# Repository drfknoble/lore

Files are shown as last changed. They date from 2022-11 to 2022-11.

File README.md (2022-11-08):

# Low-Cost, Open-Source Robot for Education (LORE)










## Introduction

Welcome to my repository for my Low-Cost, Open-Source Robot for Education (LORE) project.

<div>
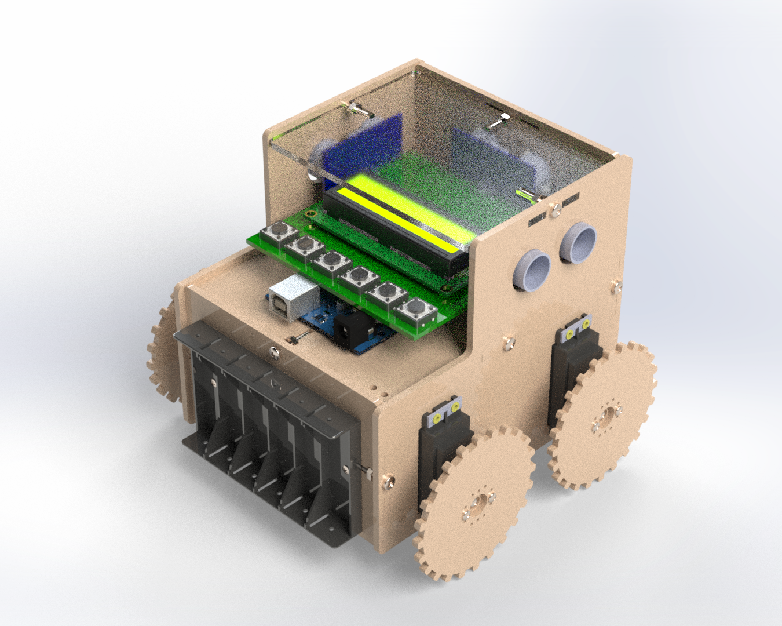
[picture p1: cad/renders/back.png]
    
    
</div>

## Motivation

I started this project because I was approached by the House of Science, a Science, Technology, Engineering, and Mathematics (STEM) organisation in Tauranga, New Zealand, who needed a low-cost, i.e., less than NZD$100.00, platform that could be used to teach robotics.

The problem was: there wasn't anything on the market at met the organisation's needs, so I decided to build one for them.

## Aims

The aims of this project included:
- Developing a low-cost, mobile robot that can be used to teach beginner, intermediate, and advanced students how to program in C++.

## Objectives

The objectives of this project included:
- Creating accessible Computer Aided Design (CAD) files.
- Creating accessible Electronics Design Automation (EDA) files.
- Creating accessible source code and software libraries.
- Creating an easy-to-assemble mobile robot that uses an Arduino microcontroller, servo motors, and ultrasonic sensors.
- Writing clear-to-follow instructions of how to program the mobile robot.

## Repository Structure

The repository is organised as follows:

```console
/lore         
    /cad                          
        /solidworks                    
        /freecad  
        /fabrication
        /renders                     
    /pcb
        /eagle
        /kicad
        /fabrication
    /src
        /beginner
        /intermediate
        /advanced
        /ROBOT
    /doc                      
        /img
        /costing                
        /programming_guide
```

All CAD files can be found in the `/cad` sub-directory. I've included the original SOLIDWORKS files and the open-source equivalents.

All EDA files can be found in the `/pcb` sub-directory. I've included the original Eagle files and the open-source equivalents.

All source code and software libaries are included in the `/src` sub-directory. The `/ROBOT` sub-directory is the Arduino library that is used to program the robot.

Documentation is included in the `/doc` sub-directory.

## Tools Used

I used the following tools in this project:
- SOLIDWORKS and FreeCAD.
- Eagle and KiCAD.
- Microsoft Visual Studio and Arduino Integrated Development IDE (IDE).

Get FreeCAD here: https://www.freecadweb.org/.  
Get KiCAD here: https://www.kicad.org/.  
Get Arduino IDE here: https://www.arduino.cc/en/software.  
Get Visual Studio here: https://visualstudio.microsoft.com/.  

Alternatively, you can use Microsoft Visual Studio Code as the IDE.

Get Code here: https://code.visualstudio.com/.

## Credit

Dr Frazer K. Noble  
http://drfknoble.com

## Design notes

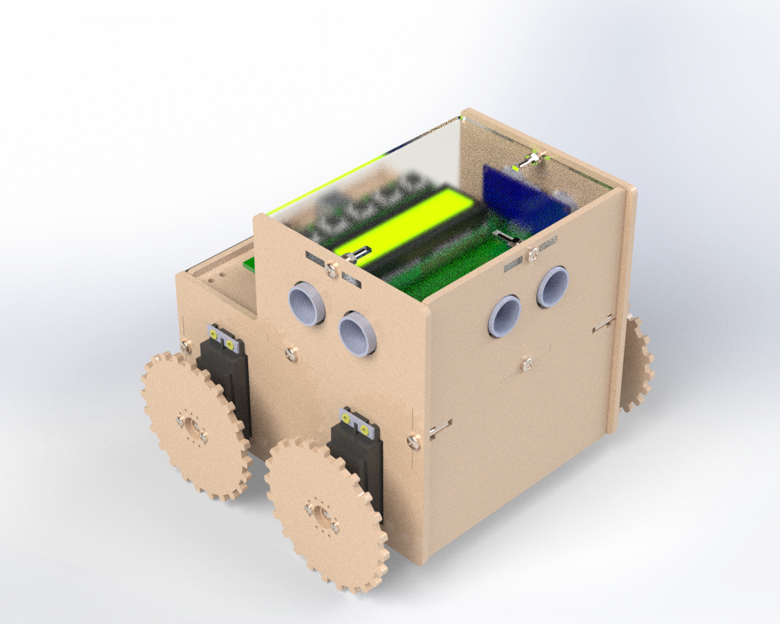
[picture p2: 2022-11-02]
cad/renders/front.png

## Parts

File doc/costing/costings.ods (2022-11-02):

Low-cost Open-source Robotics Education (LORE) kit
Item | Supplier | Number | Unit Cost (NZD) | Total Cost (NZD)
Moxie Mox-M38-360 Motors | Low Price RC | 96 | $5.00 | $480.00
MDF per robot kit | Mitre 10 Mega | 2 | $20.00 | $40.00
LCD 16x02 | Ebay | 30 | $3.00 | $90.00
Arduino Uno Rev. 3 | Ebay | 30 | $12.00 | $360.00
Ultrasonic Sensors | Ebay | 9 | $17.00 | $153.00
Tactile Switch | Ebay | 5 | $4.00 | $20.00
Header Pins | Ebay | 6 | $2.00 | $12.00
DC-DC LM2596 Converter | Ebay | 30 | $2.00 | $60.00
Battery Case | Ebay | 30 | $3.00 | $90.00
PCB | Seed Studio | 1 | $100.00 | $100.00
M3 * 15 Nuts and Bolts | EDL/Mitre 10 Mega | 8 | $5.00 | $40.00
Tools | Mitre 10 Mega | 4 | $10.00 | $40.00
Batteries | The Warehouse | 1 | $40.00 | $40.00
 |  |  | Material Cost: | $1,525.00
Beginner Kits |  | 16 | $35.00 | $560.00 | Cost: | $98.54 | RRP: | $150.00
Intermediate Kits |  | 8 | $20.00 | $160.00 |  | $83.54 |  | $125.00
Advanced Kits |  | 0 | $5.00 | $0.00 |  | $68.54 |  | $100.00
 | Total Kits: | 24 | Time Cost: | $720.00 |  |  | Total Sales: | $3,400.00
 |  |  | Total Cost: | $2,245.00 |  |  | Total Profit: | $1,155.00
Moxie M38-360 Analog Plastic Standard 360° Servo For FPV [MOX-M38-360] - $4.08USD$3.40USD Low Price RC Limited
http://www.lowpricerc.com/product_info.php/moxie-m38-360-analog-plastic-standard-360%C3%82%C2%B0-servo-for-fpv-p-745
Arduino Uno R3 Official Board Rev 3 Sense and Control LEDs Robots Electronics | eBay
http://www.ebay.com/itm/Arduino-Uno-R3-Official-Board-Rev-3-Sense-and-Control-LEDs-Robots-Electronics-/360580350466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
New DC DC LM2596 Step Down Adjustable Power Supply Module Converter DC 1 3V 35V | eBay
http://www.ebay.com/itm/New-DC-DC-LM2596-Step-Down-Adjustable-Power-Supply-Module-Converter-DC-1-3V-35V-/380755874794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
50x Tact Tactile Push Button Switch Momentary DIP Through Hole 4pin 12x12x4 3mm | eBay
http://www.ebay.com/itm/50x-Tact-Tactile-Push-Button-Switch-Momentary-DIP-Through-Hole-4pin-12x12x4-3mm-/281245791277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
10 x Ultrasonic Module HC SR04 Distance Measuring Transducer Sensor for Arduino | eBay
http://www.ebay.com/itm/10-x-Ultrasonic-Module-HC-SR04-Distance-Measuring-Transducer-Sensor-for-Arduino-/130705106799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
10pcs 40pin 2 54mm Single Row Straight Male Pin Header Strip PBC Ardunio | eBay
http://www.ebay.com/itm/10PCS-40Pin-2-54mm-Single-Row-Straight-Male-Pin-Header-Strip-PBC-Ardunio-/180974247480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
AA Battery Case 6XAA 6 AA 9V Battery Holder Battery Box with Wire Plug 5 5 2 1mm | eBay
http://www.ebay.com/itm/AA-Battery-Case-6XAA-6-AA-9V-Battery-Holder-Battery-Box-With-Wire-Plug-5-5-2-1mm-/231103696144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
1602 16x2 HD44780 Character LCD Display Module LCM Blue Blacklight New 2014 | eBay
http://www.ebay.com/itm/1602-16x2-HD44780-Character-LCD-Display-Module-LCM-blue-blacklight-New-2014-/181295337227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
AA Battery Case 6XAA 6 AA 9V Battery Holder Battery Box with Wire Plug 5 5 2 1mm | eBay
http://www.ebay.com/itm/AA-Battery-Case-6XAA-6-AA-9V-Battery-Holder-Battery-Box-With-Wire-Plug-5-5-2-1mm-/231103696144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

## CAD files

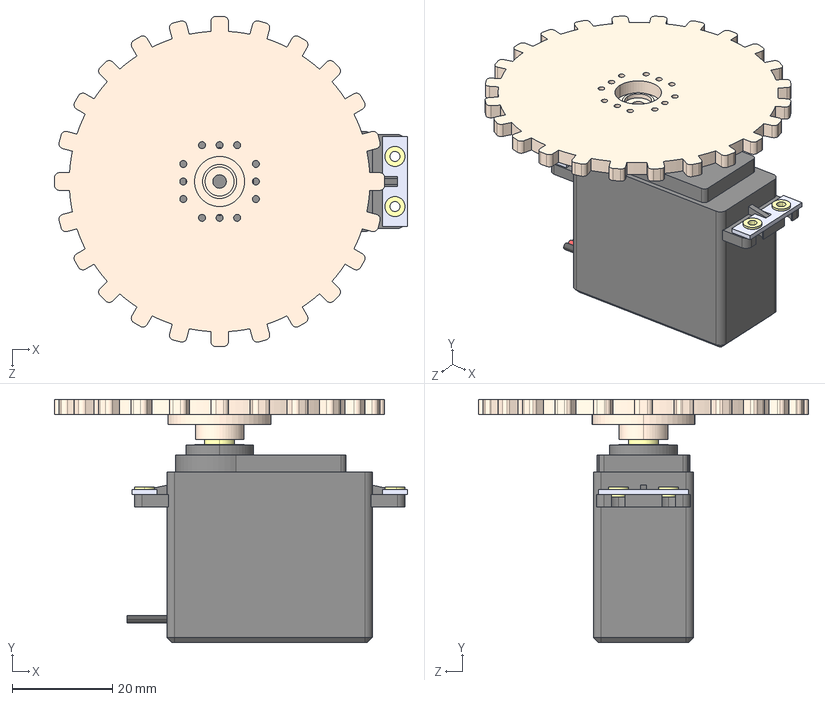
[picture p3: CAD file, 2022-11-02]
cad/freecad/sub_assemblies/motor_assembly.STEP
70.4 x 48.5 x 65.9 mm
servo_motor
servo_eyelet x 4
servo_horn
servo_mounting_rubber x 2
wheel

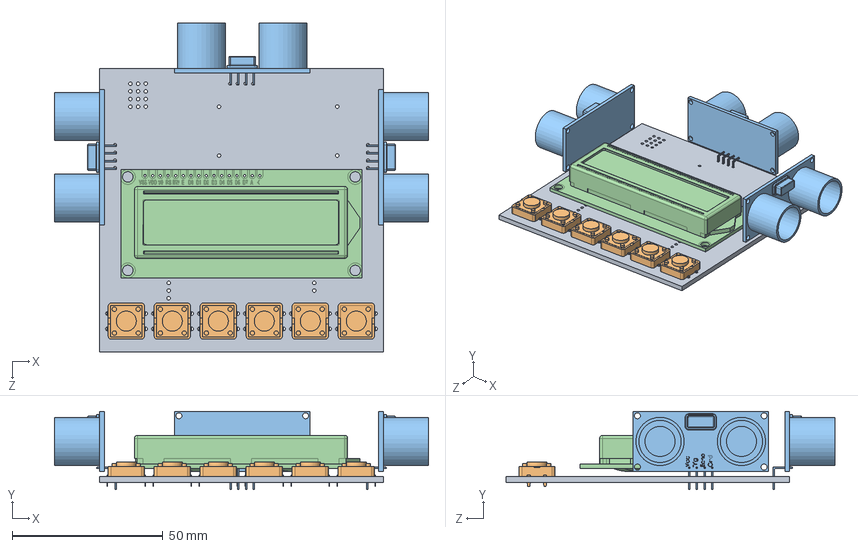
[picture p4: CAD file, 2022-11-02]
cad/solidworks/sub_assemblies/shield_assembly.SLDASM
124.0 x 26.0 x 109.0 mm
pcb
momentary_switch x 6
ultrasonic_sensor x 3
lcd1602

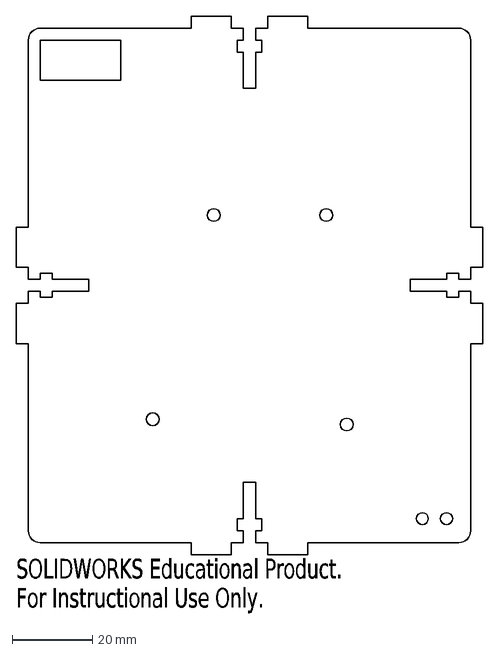
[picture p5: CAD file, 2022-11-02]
cad/fabrication/middle.DXF
SOLIDWORKS Educational Product.
For Instructional Use Only.

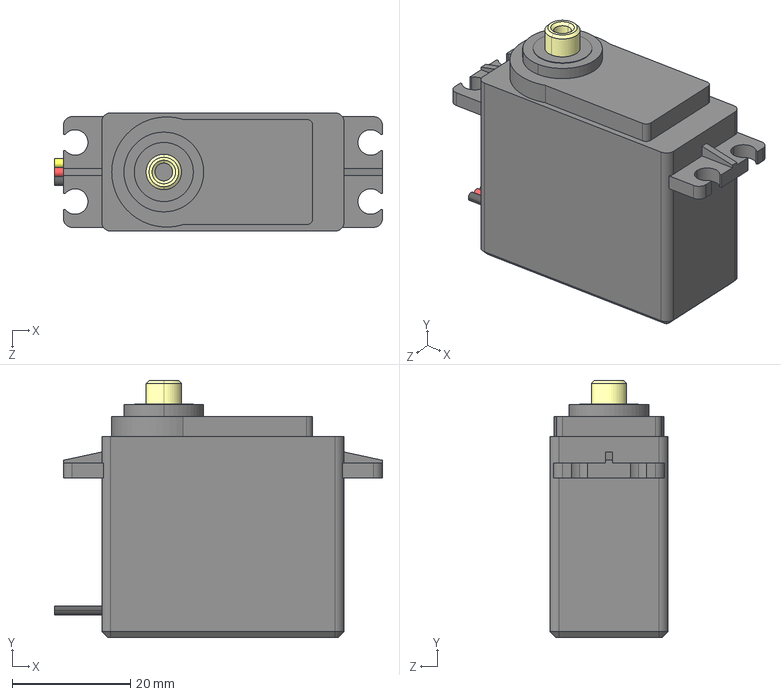
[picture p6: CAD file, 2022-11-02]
cad/freecad/parts/servo_motor.STEP
55.5 x 43.5 x 20.0 mm

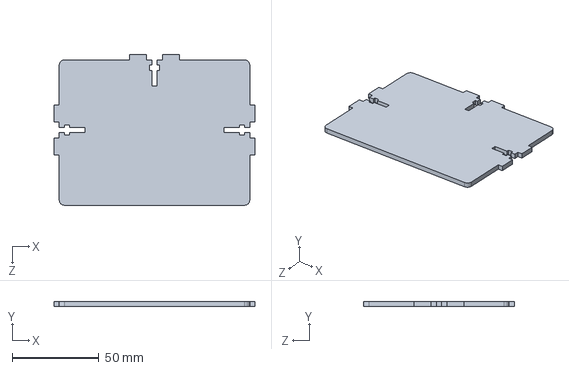
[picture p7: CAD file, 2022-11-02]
cad/solidworks/parts/top.SLDPRT
116.0 x 3.00 x 86.9 mm

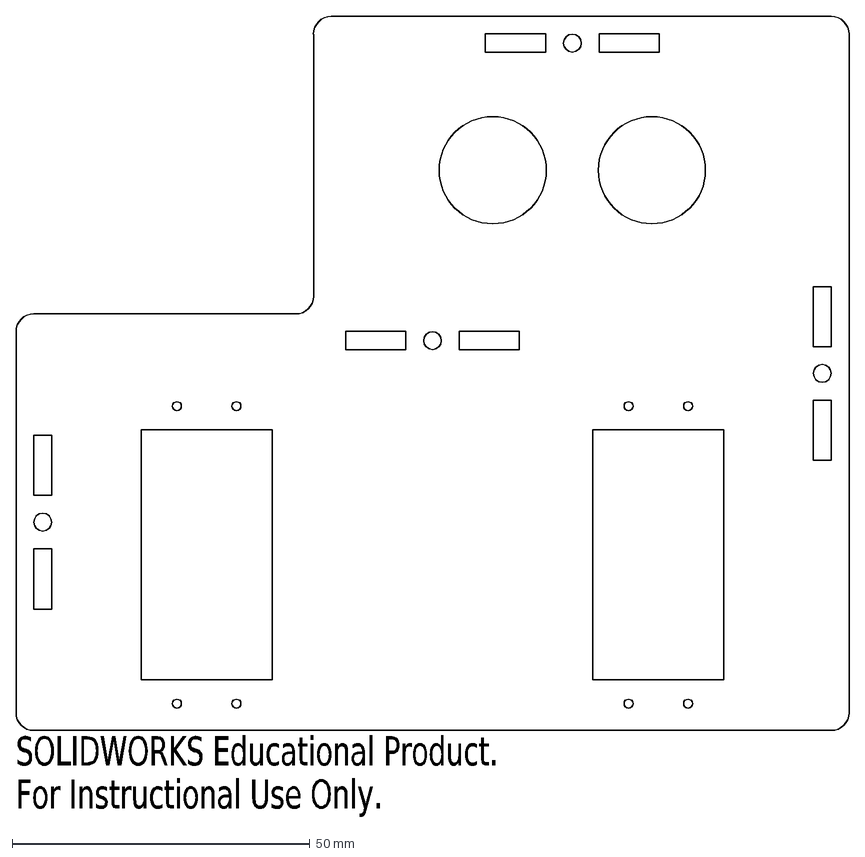
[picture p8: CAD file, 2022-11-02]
cad/fabrication/side.DXF
SOLIDWORKS Educational Product.
For Instructional Use Only.

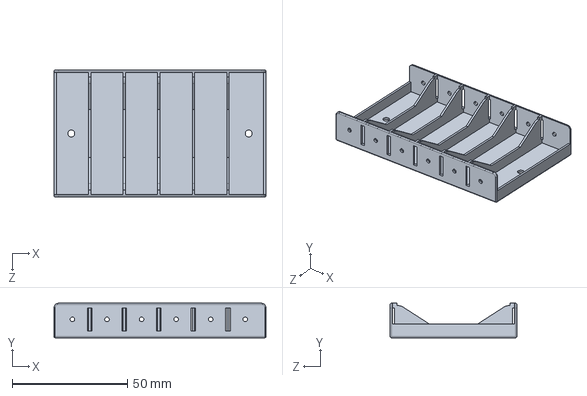
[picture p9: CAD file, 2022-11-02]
cad/freecad/parts/battery_clip.STEP
92.0 x 15.0 x 55.0 mm

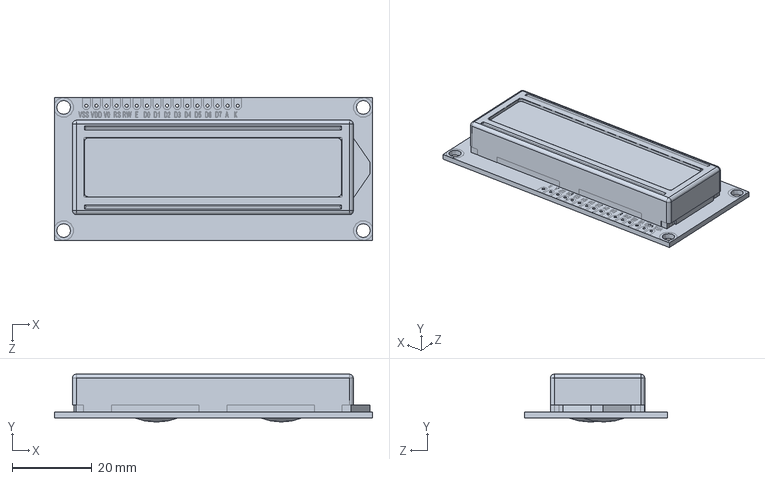
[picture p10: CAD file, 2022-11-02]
cad/solidworks/parts/lcd1602.SLDPRT
80.0 x 12.1 x 36.0 mm

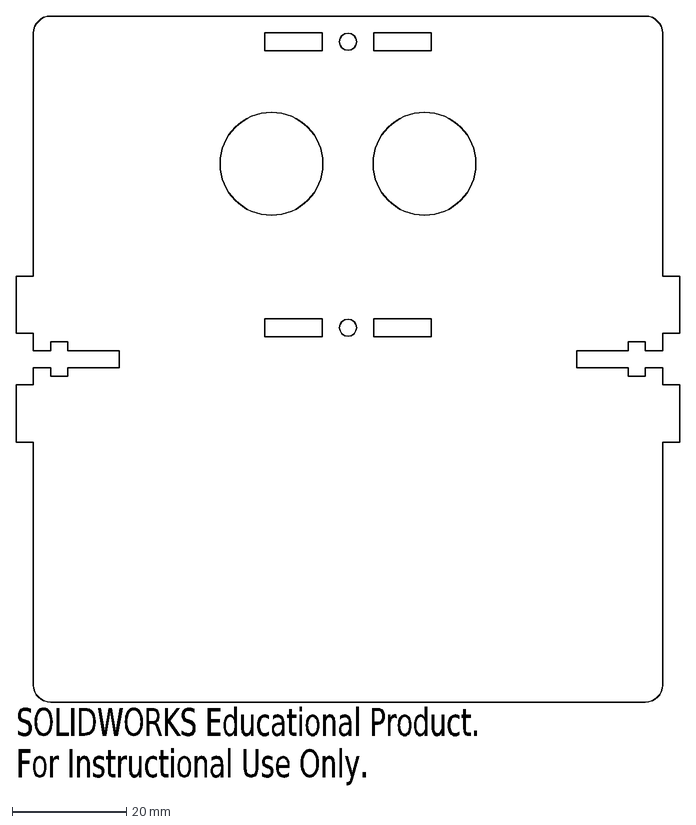
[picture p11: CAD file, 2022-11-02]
cad/fabrication/front.DXF
SOLIDWORKS Educational Product.
For Instructional Use Only.

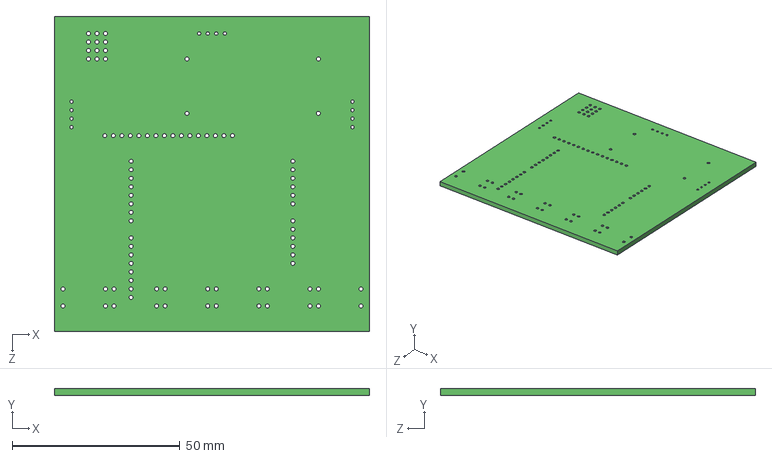
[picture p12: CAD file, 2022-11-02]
cad/freecad/parts/pcb.STEP
94.0 x 2.00 x 94.0 mm

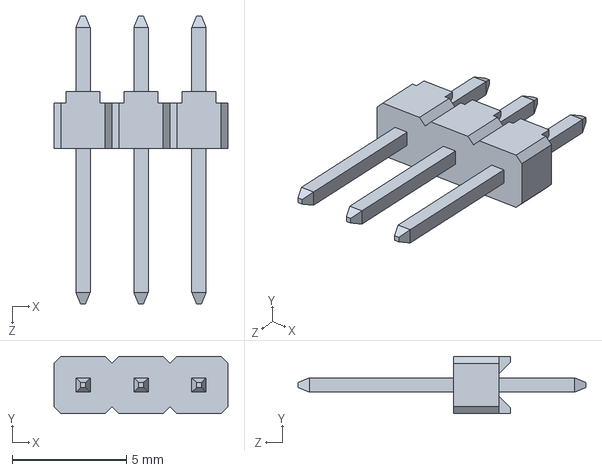
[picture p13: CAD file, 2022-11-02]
cad/solidworks/parts/3_pin_header.SLDPRT
7.62 x 2.50 x 12.6 mm

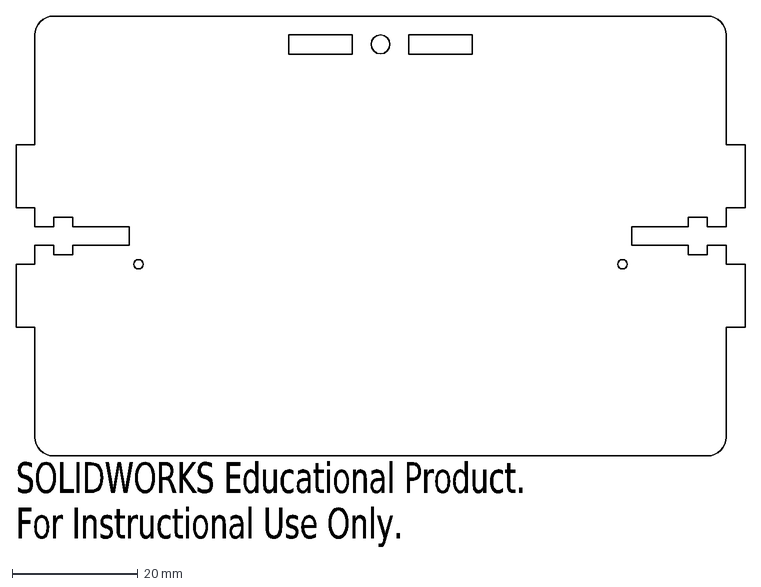
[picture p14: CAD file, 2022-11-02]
cad/fabrication/back.DXF
SOLIDWORKS Educational Product.
For Instructional Use Only.

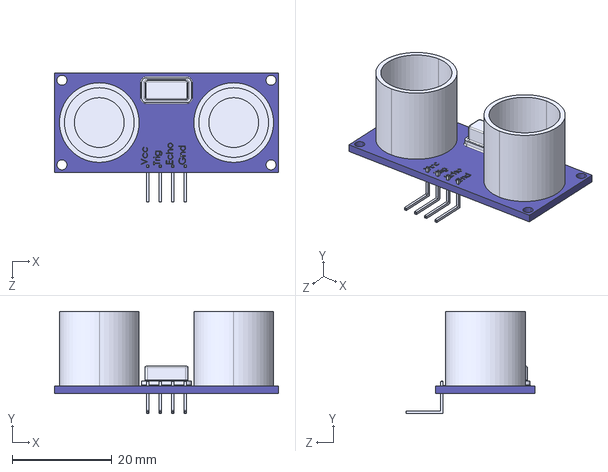
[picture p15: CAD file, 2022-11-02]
cad/freecad/parts/ultrasonic_sensor.STEP
45.0 x 20.5 x 26.0 mm

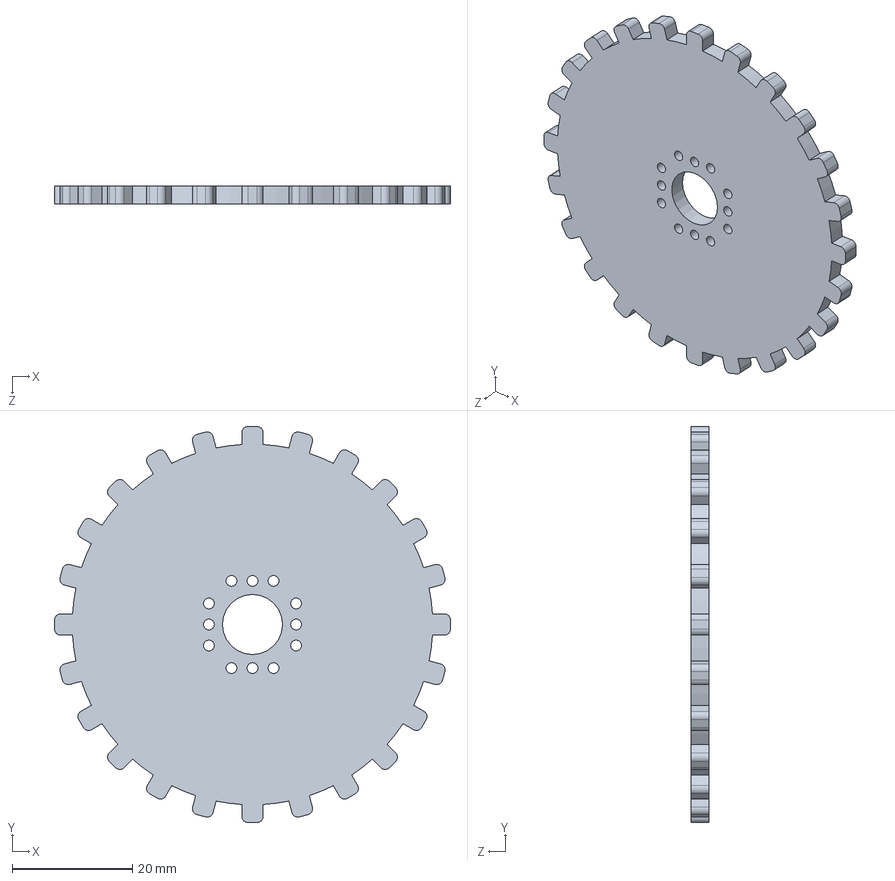
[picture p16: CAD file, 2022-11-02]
cad/solidworks/parts/wheel_alt.sldprt
65.9 x 65.9 x 3.00 mm

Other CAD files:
cad/freecad/parts/servo_eyelet.STEP
cad/freecad/parts/momentary_switch.STEP
cad/freecad/parts/back.STEP
cad/freecad/parts/front.STEP
cad/freecad/parts/middle.STEP
cad/freecad/parts/servo_horn.STEP
cad/freecad/parts/servo_mounting_rubber.STEP
cad/freecad/parts/side.STEP
cad/freecad/parts/wheel.STEP
cad/solidworks/parts/back.SLDPRT
cad/solidworks/parts/battery_clip.SLDPRT
cad/solidworks/parts/front.SLDPRT
cad/solidworks/parts/middle.SLDPRT
cad/solidworks/parts/momentary_switch.SLDPRT
cad/solidworks/parts/pcb.SLDPRT
cad/solidworks/parts/servo_eyelet.SLDPRT
cad/solidworks/parts/servo_horn.SLDPRT
cad/solidworks/parts/servo_motor.SLDPRT
cad/solidworks/parts/servo_mounting_rubber.SLDPRT
cad/solidworks/parts/side.SLDPRT
cad/solidworks/parts/ultrasonic_sensor.SLDPRT
cad/solidworks/parts/wheel.sldprt
cad/solidworks/sub_assemblies/motor_assembly.SLDASM

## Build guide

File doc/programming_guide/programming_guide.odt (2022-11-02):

Disclaimer: Low-cost Open-source Robotics Educational (LORE) kits are provided "as is" with no warranties whatsoever, including any warranty of merchantability, non - infringement, fitness for any particular purpose, or any warranty otherwise arising out of any proposal, specification or sample. LORE kits (and manufacturers and distributors) disclaim all liability, including liability for infringement of any proprietary rights, relating to use of information in any documents and files and software and no license, express or implied, by LORE kits or otherwise, to any intellectual property rights is granted herein. LORE kits (and manufacturers and distributors) assumes no responsibility or liability for any errors or inaccuracies that may appear in any documentation or files or any software that may be provided. The information in any documents or files is furnished for informational use only, is subject to change without notice, and should not be construed as a commitment by LORE kits (and manufacturers and distributors).

# Table of Figures

Figure 1: Beginning Programming Level procedure. 2

Figure 2: Arduino Uno R3 Board 3

Figure 3: Intermediate Programming Level procedure. 6

Figure 4: Advanced Programming Level procedure. 9

# Editions

Edition 1.

Edition 1.01. Added introductory programming examples, i.e. Getting Started. Added additional information regarding new functions, e.g. turn() and setTurnTime().

# Low-Cost Open-Source Robotics Education (LORE) kit Programming Guide:

Programming the LORE robot can be broken into three levels of difficulty:

- Beginner Programming Level. Suitable for students with no programming experience. No computer experience required.
- Intermediate Programming Level. Suitable for students with some programming knowledge. Students should be familiar with computers and how to use an Internet browser, keyboard and mouse.
- Advanced Programming Level. Suitable for students with programming experience in C/C++. Students should be computer literate and familiar with Windows 7/8.

To familiarise students with programming, the following section provides a primer on programming.

# Programming Primer:

There are a number of excellent resources for learning to program, e.g. LearnCpp.com. Here, we provide a very basic, and limited, introduction to some key concepts: variables and functions, which are used in the Intermediate and Advanced Programming Levels.

For a complete introduction to variables and functions, see the tutorials available from LearnCpp:

http://www.learncpp.com.

Variables:

“A variable in C/C++ is a name for a piece of memory that can be used to store information” (C++, 2014). A variable can be thought of as a box, where information can be put.

Here’s an example of declaring an integer variable:

int x = 0;

The variable’s name is x and is set to zero. Keyword int sets the variable type to integer. The equal sign is used to specify what integer x is equal to. The number zero sets x’s value.

For a complete list of variable types, see the following link:

http://en.wikipedia.org/wiki/C_data_types

Functions:

“A function is a sequence of statements designed to do a particular job” (C++, 2014). In C/C++, every program requires a main() function; however, for Arduino boards, there must be a setup() function and a loop() function.

Here’s an example of declaring a function:

void print(char* string) {

Serial.print(string);

}

The function’s name is print. Function print() takes a single parameter: string, which is an array of characters. Function print() calls the print() member function, or method, of an instance of a Serial Port class, Serial. Function print() does not return any value; however, functions can return any standard data type.

# Beginner Programming Level Guide:

The Beginner Programming Level is suitable for students that have no prior knowledge of programming. Programming the LORE robot is done by pressing the PROGRAM button followed by pressing a series of LEFT, RIGHT, FRONT, and BACKWARD directional buttons. Once a program is finished, pressing the SELECT button saves the program. Each time the directional buttons are pressed, the LCD panel will display the button pressed. By default the maximum program size is 50 steps; however, this can be changed. When the program is full, the LCD will display “PROGRAM FULL”. Pressing the SELECT button a second time executes the program. The program will run through each pre-programmed step until it is finished. By default, each step will execute for one second (FORWARD and BACKWARD movements) or 90 ° (LEFT or RIGHT turns). Pressing the SELECT button will re-run the program. Pressing the PROGRAM button again will re-enter programming mode. When re-entering programming mode, the previous program is overwritten.

The following figure (Figure 1) outlines the Beginner Programming Level structure:

Press the PROGRAM button.

Press the PROGRAM button to enter programming mode.

↓

Enter the PROGRAM.

Press the LEFT, RIGHT, FORWARD, or BACKWARD buttons.

Repeat this step till desired movements are loaded.

↓

Press the SELECT button.

Press the SELECT button to save the program.

↓

Press the SELECT button.

Press the SELECT button to run the program.

↓

Wait for program to run.

Figure 1: Beginning Programming Level procedure.

## Beginner Programming Level Example 1:

Consider a student, Marty, who wants to make the LORE robot move forward for 10 seconds, turn left, move forward for two seconds, and then stop.

To program the LORE robot to do this, the student should do the following:

1. Press the PROGRAM button. This will enter programming mode.
2. Press the FORWARD button. This will make the LORE robot move forward for one second.
3. Repeat Step 2 9 more times. Pressing the FORWARD button an additional nine more times will program the robot to move forward for an additional nine seconds.
4. Press the LEFT button. This will make the robot turn 90 ° to the left.
5. Press the FORWARD button. This will make the LORE robot move forward for one second.
6. Repeat Step 5 one more time. Pressing the FORWARD button one more time will program the robot to move forward for an additional one second.
7. Press the SELECT Button.

To run the program, the student should press the SELECT button again.

# Intermediate Programming Level Guide:

The Intermediate Programming Level is suitable for students who have some prior knowledge of programming and are familiar with computers, i.e. able to use a mouse and keyboard for typing and data entry in a Windows 7/8 environment, as well as, browsing the Internet using an Internet browser. Students are provided with a simple set of functions, which they can call to program the robot to move (FORWARD and BACKWARD) and turn 90 ° (LEFT and RIGHT). Students can also access the LORE robot’s FRONT SENSOR, LEFT SENSOR, and RIGHT SENSOR ultrasonic sensors to measure distances from the robot.

## Getting Started:

Before being able to program the robot, students will need to download the Arduino integrated development environment (IDE) and the ROBOT library file. The IDE can be downloaded for free from the following site:

http://arduino.cc/

Browse to the Download section and download the latest, stable version: as of May, 2014 it is version 1.0.5. The Windows Installer will automatically install all the software and drivers necessary to program the LORE robot’s microcontroller: the Arduino Uno. By default the IDE will install to C:\Progam Files\Arduino; however, you may install this to any directory. When installing the Arduino IDE you will need administrator rights to install software and driver. For supplementary instructions on installing the Arduino IDE, refer to the Arduino website.

Once the Arduino IDE is installed, you can make use of a library created for the LORE robot and the Arduino board. Download ROBOT.zip from the following link:

https://sourceforge.net/projects/lorerobotics/files/.

Extract ROBOT.zip to the Arduino user library folder. To extract the file, right click the file and left click Extract All…. By default the Arduino user library folder will be in the default Arduino workspace within the documents directory, e.g. C:\Users\...\Documents\Arduino\libraries (NB. “…” corresponds to the current user name; this will differ from machine to machine).

To use the library, open the Arduino IDE and left click Select>Add Library…>ROBOT. If ROBOT.zip has been extracted to the correct file, the library ROBOT will be listed under the Contributed libraries.

## Programming the Arduino Board:

The Arduino board is a simple-to-use and easy-to-program development board. The LORE robot uses the Uno model (see Figure 2).

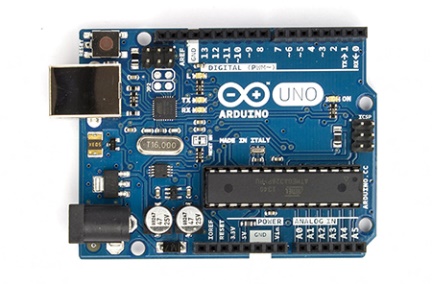
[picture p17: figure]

Figure 2: Arduino Uno R3 Board

For tutorials on programming Arduinos, have a look at the following link:

http://arduino.cc/en/Tutorial/HomePage

At the least, the following code is necessary for programming the Arduino board:

void setup()

{

// put your setup code here, to run once:

}

void loop()

{

// put your main code here, to run repeatedly:

}

The setup() function is called when a sketch starts. Use it to initialize variables, pin modes, start using libraries, etc. The setup function will only run once, after each power up or reset of the Arduino board. After creating a setup() function, which initializes and sets the initial values, the loop() function does precisely what its name suggests, and loops consecutively, allowing your program to change and respond. Use it to actively control the Arduino board. Program logic should be placed in loop(), which will continuously execute the program.

Intermediate Programming Level Tip 1:

When uploading the programme to the LORE robot’s Arduino, you’ll need to identify which COM port to use. Typically COM 1/2 refers to the hardware serial ports on older machines, so you’ll find the Arduino’s COM port will be COM 3 or higher. You can be sure which COM port it is by using Window’s Device Manager. This can be found by pressing the Windows Start key and typing “Device Manager”, then selecting Device Manager under the found items. Browsing to the Ports (COM & LPT) menu and expanding it, you can see what the Arduino’s COM port is.

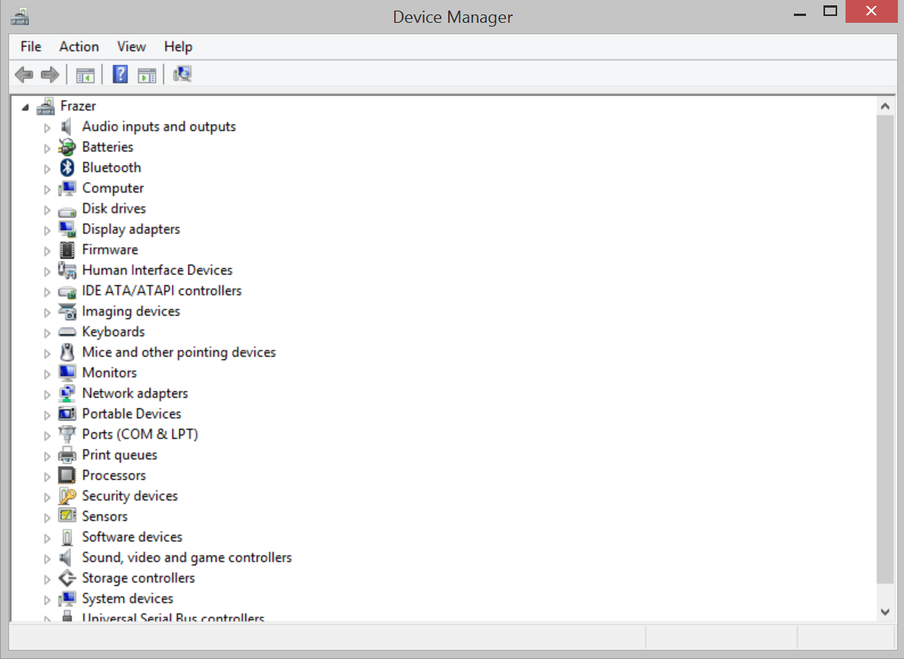
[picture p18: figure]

Figure 3: Windows Device Manager. (Insert) Drop down menu showing which port the Arduino is connected to.

## Using the ROBOT Library:

The ROBOT library provides a number of easy-to-use functions that allow for the LORE robot to be controlled. The ROBOT library functions are as follows:

- bool initialise(). The initialise() function sets all the Arduino board’s pins direction (INPUT or OUTPUT) and sets their states (HIGH or LOW). When the robot is initialised, the function returns TRUE.
- bool buttonPressed(int button) . The buttonPressed() function is used to see if one of the LORE robot’s buttons have been pressed. If the button is pressed, the function buttonPressed returns TRUE; else, it returns FALSE.
- bool clear(). The clear() function clears the LORE robot’s program. When the robot’s program is cleared, the function returns TRUE.
- bool move(int direction) . The move() function moves the LORE robot in a specific direction (FORWARD or BACKWARD): parameter direction specifies the movement it makes. When move finished, the function returns TRUE. If direction is not FORWARD or BACKWARD, move() returns FALSE.
- bool turn(int direction). The turn() function turns the LORE robot in a specific direction (LEFT and RIGHT): the parameter direction defines the turn it makes. When turn() finished, the function returns TRUE. If direction is not LEFT or RIGHT, turn() returns FALSE.
- bool setTurnTime(int direction, int time). The setTurnTime() sets the time the robot turns in a specific direction (LEFT or RIGHT) for a specific time: the parameter direction defines which turn and parameter time specifies for how long. When setTurnTime() finished, the function returns TRUE. If direction is not LEFT or RIGHT, setTurnTime() returns FALSE.
- bool program(int direction) . The program() function allows the LORE robot to be programmed in a similar way to the beginner programming use-case. If the program size is less than 50, the function returns TRUE for successfully programming direction = LEFT | RIGHT | FORWARD | BACKWARD; else, it returns FALSE.
- bool run(). The run() function runs the program set using the program function. If program size is greater than zero, the function returns TRUE; else, it returns FALSE.
- bool writeLCD(char* string) . The writeLCD() function prints a series of characters to the LORE robot’s LCD panel. The maximum number of characters that can be shown is 16. If the string is not empty, the function returns TRUE on completion; else, it returns FALSE.
- long measureDistance(int sensor). The measureDistance() function samples the LORE robot’s ultrasonic sensors. If the robot successfully makes a measurement, measureDistance() returns the distance in centimetres; else, it returns -1;

All these functions are provided via a class. To access these functions, create an instance of the ROBOT class. For example:

ROBOT marty;

Here, marty is the name of the instance of the ROBOT class. Think of the ROBOT describing the LORE robot and the instance, i.e. marty, the name of the specific robot. The instance could be called anything sensible, e.g. Judy, mark, WALLE, etc. Only one instance needs to be used to control the LORE robot.

To gain access to the initialise(), buttonPressed(), clear(), move(), program(), run(), and writeLCD() functions, you need to add ‘ . ’ to the instance name and type the function name. For example:

marty.initialise();

marty.buttonPressed(PROGRAM);

marty.clear();

marty.move(FORWARD);

marty.program(FORWARD);

marty.run();

marty.writeLCD("HELLO");

Note, for buttonPressed() and and program(), the acceptable inputs are: PROGRAM, SELECT, LEFT, RIGHT, FORWARD, and BACKWARD. Only these keywords will work.

For move(), the acceptable inputs are: LEFT, RIGHT, FORWARD, and BACKWARD. Only these keywords will work.

For writeLCD(), you can print any string of characters (as long as they’re English and the string length is less than 16).

The following figure (Figure 4) outlines the intermediate programming structure:

Open the Arduino IDE.

Open the Arduino IDE.

↓

Add the ROBOT library.

Left click Select>Add Library…>ROBOT.

This will add the Servo, LiquidCrystal, and ROBOT header files automatically.

↓

Enter the program.

First, create an instance of the ROBOT class; next, Using initialise(), buttonPressed(), clear(), move(), program(), run(), and writeLCD(), program the robot to carry out a desired set of movements, read data from sensors, and wait for input from the user.

↓

Upload the program to the LORE robot.

Turn on the LORE robot and plug in the USB cable. Press Upload in the Arduino IDE.

↓

Wait for program to run.

Figure 4: Intermediate Programming Level procedure.

## Intermediate Programming Level Example 1:

Consider a student, Marty, who wants to make the LORE robot move forward for 10 seconds, turn left, move forward for two seconds, and then stop.

To program the LORE robot to do this, the student should do the following:

1. Open the Arduino IDE.
2. Add the ROBOT library.
3. Enter the following program:

#include <ROBOT.h>

#include <Servo.h>

#include <LiquidCrystal.h>

ROBOT marty;

void setup()

{

marty.initialise();

}

void loop()

{

if (marty.buttonPressed(PROGRAM)) {

marty.move(FORWARD);

marty.move(FORWARD);

marty.move(FORWARD);

marty.move(FORWARD);

marty.move(FORWARD);

marty.move(FORWARD);

marty.move(FORWARD);

marty.move(FORWARD);

marty.move(FORWARD);

marty.move(FORWARD);

marty.move(LEFT);

marty.move(FORWARD);

marty.move(FORWARD);

}

}

Here, we created an instance of the ROBOT class named marty. Then we initialised marty using the initialise() function. We then checked to see if the PROGRAM button was pressed; if it was, we made the LORE robot move; else, we waited till the PROGRAM button is pressed.

4. Upload the program to the LORE robot.

Once the program has been uploaded to the LORE robot’s Arduino board, the program will begin to execute immediately.

Intermediate Programming Level Tip 2:

When writing a program for the LORE robot, don’t forget to use the robot’s buttons. You can make the robot wait for you to press a button, if you don’t want it to run your program straight away.

Intermediate Programming Level Example 2:

Consider the same student, Marty, who now wants to make the LORE robot move forward for 10 seconds, but stop if an object is 20 cm in front of the robot.

To program the LORE robot to do this, Marty should do the following:

1. Open the Arduino IDE.
2. Add the ROBOT library.
3. Enter the following program:

#include <ROBOT.h>

#include <Servo.h>

#include <LiquidCrystal.h>

ROBOT marty;

void setup()

{

marty.initialise();

}

void loop()

{

if (robot.buttonPressed(PROGRAM)) {

for (int i = 0; i < 10; i++) {

marty.move(FORWARD);

long distance = 0;

distance = marty.measureDistance(FRONT_SENSOR);

if (distance <= 20) {

break;

}

}

}

}

Here, we created an instance of the ROBOT class named marty. Then we initialised marty using the initialise() function. We then checked to see if the PROGRAM button was pressed; if it was, we made the LORE robot move FORWARD for 10 seconds; else, we waited till the PROGRAM button is pressed. If the FRONT_SENSOR measured a distance less than or equal to 20 cm, the robot stopped moving.

4. Upload the program to the LORE robot.

Once the program has been uploaded to the LORE robot’s Arduino board, the program will begin to execute immediately.

# Advanced Programming Level Guide

The Advanced Programming Level is suitable for students with programming experience in C/C++. Students should be computer literate and familiar with Windows 7/8. The Advanced Programming Level builds upon the Intermediate Programming Level. Students should download the Arduino IDE, as discussed in the Intermediate Programming Level instructions; however, it is not necessary for them to use the ROBOT library as the template provided provides the same functionality, but uses standard Arduino and C-based functions.

At this level, students should use the Arduino board’s standard functions, e.g. pinMode(), digitalRead(), digitalWrite(); as well as, control structures, e.g. if, if…else, for, while, and break, as outlined on Arduino’s reference site:

http://arduino.cc/en/Reference/HomePage.

The following functions will allow for direct control of the Arduino board’s pins:

- void pinMode(int pin). The pinMode() function defines whether an Arduino board’s pin is either an INPUT or an OUTPUT pin. Data is read from an INPUT; data is written to an OUTPUT.
- void digitalWrite(int pin, int value). The digitalWrite() function sets the state of an Arduino board’s pin to either HIGH or LOW, which equates to 1 or 0, respectively.
- bool digitalRead(int pin). The digitalRead() function reads the state of an INPUT pin, returning HIGH if the voltage on the pin is greater than 2.5 V; else, it returns LOW.

Advanced Programming Level Tip 1:

The LORE robot makes use of internal 10 k Ω pull-up resistors, which means the state of the digital pins will normally be HIGH. To read if a button is pressed, check if the pin’s state is LOW, e.g. if(digitalRead(FORWARD) == LOW){ }.

Advanced Programming Level Tip 2:

To enable the LORE robot’s internal 10 k Ω pull-up, set the Arduino board’s pins to INPUTs and set them HIGH, e.g. pinMode(FORWARD, INPUT); digitalWrite(FORWARD, HIGH);

The following figure (Figure 5) outlines the intermediate programming structure:

Open the Arduino IDE.

Open the Arduino IDE.

↓

Enter the program.

Use the Advanced Programming Level template.

Using the functions move(), readButton(), and readSensor(), program the LORE robot to execute a desired set of movements. Initialise

↓

Upload the program to the LORE robot.

Turn on the LORE robot and plug in the USB cable. Press Upload in the Arduino IDE.

↓

Wait for program to run.

Figure 5: Advanced Programming Level procedure.

## Advanced Programming Level Template:

Consider a student, Marty, who now wants to program the robot (at a more advanced level) himself; rather than use the ROBOT library.

To program the LORE robot, Marty should use the following template:

/*

Headers. Header files are declared here. The #include keyword is used to include a *.h header file.

*/

#include <Servo.h>

#include <LiquidCrystal.h>

/*

Defines. Defines are declared here. Defines aren't variables; rather they're statements which replace key words with values when the program is compiled.

*/

#define BACKWARD 7

#define FORWARD 8

#define RIGHT 9

#define LEFT 10

#define SELECT 11

#define PROGRAM 12

#define RS A0

#define E A1

#define D4 A2

#define D5 A3

#define D6 A4

#define D7 A5

#define FRONT_SENSOR 2

#define LEFT_SENSOR 3

#define RIGHT_SENSOR 4

#define LEFT_MOTORS 5

#define RIGHT_MOTORS 6

/*

Global Variables. Global variables are declared here. Format: variableType variableName; or variableType variableName = defaultValue;

*/

long debounceDelay = 50;

long programDebounceTime = 0;

long selectDebounceTime = 0;

long leftDebounceTime = 0;

long rightDebounceTime = 0;

long forwardDebounceTime = 0;

long backwardDebounceTime = 0;

int programState = HIGH;

int programPrevState = HIGH;

int selectState = HIGH;

int selectPrevState = HIGH;

int leftState = HIGH;

int leftPrevState = HIGH;

int rightState = HIGH;

int rightPrevState = HIGH;

int forwardState = HIGH;

int forwardPrevState = HIGH;

int backwardState = HIGH;

int backwardPrevState = HIGH;

long frontSensorValue = 0;

long leftSensorValue = 0;

long rightSensorValue = 0;

char programString[50] = {};

int programSet = 0;

int programSize = 0;

/*

Class instances. Class objects are declared here.

*/

LiquidCrystal lcd(RS, E, D4, D5, D6, D7);

Servo leftMotors, rightMotors;

/*

Function Declarations. Function prototypes are declared here. Format: returnType functionName(parameterType parameterName, ...);

The function contents are defined after void loop().

*/

bool move(int direction);

bool readButton(int button, int &buttonState, int &buttonPrevState, long &debounceTime);

bool readSensor(int sensor, long &distance);

/*

Function: void setup().

Returns: None.

Parameters: None.

Description: Setup initialises the program's variables. Here the pinMode’s of the PROGRAM through to BACKWARD buttons are set as inputs and then internal pull up resistors enables by writing a HIGH logic level to the buttons' associated pins. Sensors are configured as outputs and their states set to the LOW logic level. Servo motors are attached to LEFT_MOTORS and RIGHT_MOTORS pins and set to a neutral position. Lastly, the serial port is opened using a default baud rate of 9600 and 8N1 parameters (8 data-bits, no parity, 1 stop bit).

*/

void setup()

{

// Initialise the LCD screen. Set size at 16 channels x 2 rows.

lcd.begin(16, 2);

lcd.clear();

lcd.home();

// Initialise the pushbuttons. Enable internal pull-ups. Logic LOW = button pressed; else HIGH.

pinMode(PROGRAM, INPUT);

digitalWrite(PROGRAM, HIGH);

pinMode(SELECT, INPUT);

digitalWrite(SELECT, HIGH);

pinMode(LEFT, INPUT);

digitalWrite(LEFT, HIGH);

pinMode(RIGHT, INPUT);

digitalWrite(RIGHT, HIGH);

pinMode(FORWARD, INPUT);

digitalWrite(FORWARD, HIGH);

pinMode(BACKWARD, INPUT);

digitalWrite(BACKWARD, HIGH);

// Initialise the sensors. Configure as outputs to start with.

pinMode(FRONT_SENSOR, OUTPUT);

digitalWrite(FRONT_SENSOR, LOW);

pinMode(LEFT_SENSOR, OUTPUT);

digitalWrite(LEFT_SENSOR, LOW);

pinMode(RIGHT_SENSOR, OUTPUT);

digitalWrite(RIGHT_SENSOR, LOW);

// Initialise servo motors.

leftMotors.attach(LEFT_MOTORS);

leftMotors.write(127);

rightMotors.attach(RIGHT_MOTORS);

rightMotors.write(127);

}

/*

Function: void loop().

Returns: None.

Parameters: None.

Description: Loops continuously, executing program logic.

*/

void loop()

{

}

/*

Function: bool drive(int direction).

Returns: bool.

Parameters: int direction.

Description: Reads in the direction the robot needs to move in. If direction is FORWARD, read front sensor and drive for 1000 ms. If sensorValue is less than a threshold, stop and move onto next instruction. If direction is !FORWARD, move for 1000 ms.
*/

bool move(int direction) {

if (direction == FORWARD) {

leftMotors.write(0);

rightMotors.write(255);

unsigned long time = 0;

time = millis();

while ((millis() - time) < 1000) {

readSensor(FRONT_SENSOR, frontSensorValue);

if (frontSensorValue < 5) {

break;

}

}

leftMotors.write(127);

rightMotors.write(127);

return true;

}

else if (direction == BACKWARD) {

leftMotors.write(255);

rightMotors.write(0);

delay(1000);

leftMotors.write(127);

rightMotors.write(127);

return true;

}

else if (direction == LEFT) {

leftMotors.write(255);

rightMotors.write(255);

delay(900);

leftMotors.write(127);

rightMotors.write(127);

return true;

}

else if (direction == RIGHT) {

leftMotors.write(0);

rightMotors.write(0);

delay(900);

leftMotors.write(127);

rightMotors.write(127);

return true;

}

return false;

}

/*

Function: bool readButton(int button, int &buttonState, int &buttonPrevState, long &debounceTime).

Returns: bool.

Parameters: int button, int &buttonState, int &buttonPrevState, long &debounceTime.

Description:

*/

bool readButton(int button, int &buttonState, int &buttonPrevState, long &debounceTime) {

int reading = digitalRead(button);

if (reading != buttonPrevState) {

debounceTime = millis();

}

if ((millis() - debounceTime) > debounceDelay) {

if (reading != buttonState) {

buttonState = reading;

if (buttonState == LOW) {

return true;

}

}

}

buttonPrevState = reading;

return false;

}

/*

Function: bool readSensor(int sensor, long &distance).

Returns: bool.

Parameters: int sensor, long &distance.

Description:

*/

bool readSensor(int sensor, long &distance) {

pinMode(sensor, OUTPUT);

digitalWrite(sensor, LOW);

delay(10);

digitalWrite(sensor, HIGH);

delay(10);

pinMode(sensor, INPUT);

int value = 0;

value = pulseIn(sensor, HIGH);

distance = value / 29 / 2;

if (distance != 0) {

return true;

}

return false;

}

In this template, the defines, e.g. #define BACKWARD 7, map keywords to a pin number. These numbers correspond to the pins on the LORE robot’s Arduino board and the PROGRAM, SELECT, LEFT, RIGHT, FORWARD, and BACKWARD buttons; the LCD panel’s data pins; and the FRONT_SENSOR, LEFT_SENSOR, and RIGHT_SENSOR data pins. The advantage of using #define is that it makes it easier to know what pin is associate to what button, etc.

The global variables, e.g. debounceDelay, programDebounceTime, programState, and programPrevState, are used to de-bounce the PROGRAM, SELECT, LEFT, RIGHT, FORWARD, and BACKWARD buttons. The variables frontSensorValue, leftSensorValue, and rightSensorValue are used to store the data measured from the LORE robot’s FRONT_SENSOR, LEFT_SENSOR, and RIGHT_SENSOR.

# Bibliography

C++, L. (2014, May 30). Learn C++. Retrieved from Learn C++ A First Look at Variables: http://www.learncpp.com/cpp-tutorial/13-a-first-look-at-variables/

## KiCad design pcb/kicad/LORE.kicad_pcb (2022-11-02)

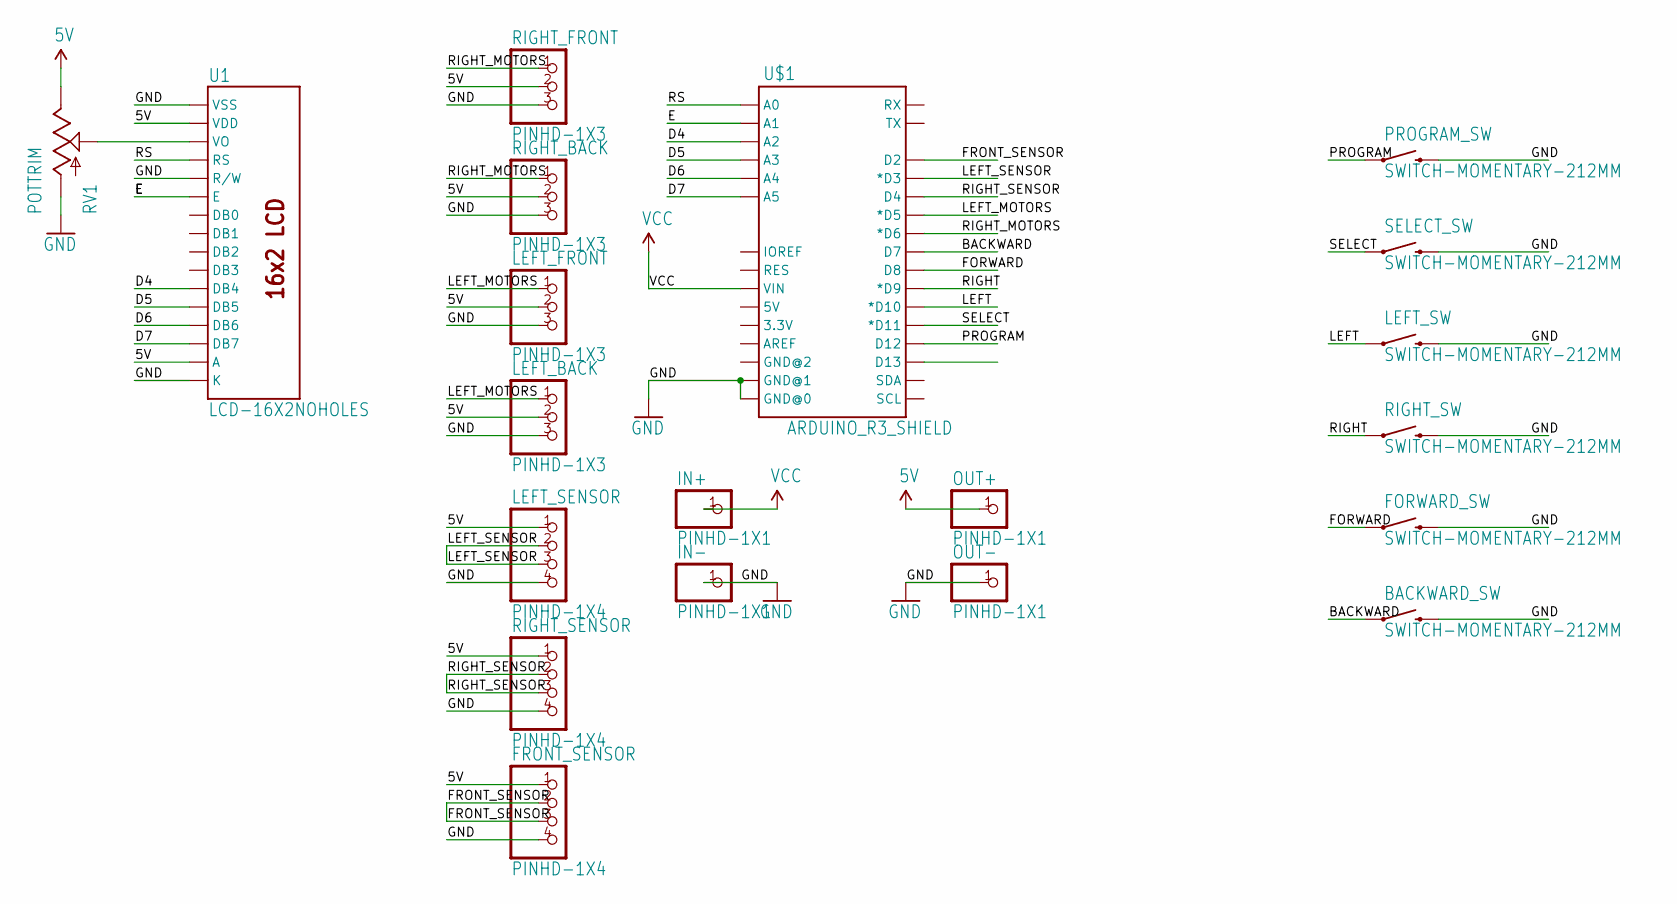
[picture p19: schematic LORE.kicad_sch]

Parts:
BACKWARD_SW: SWITCH-MOMENTARY-212MM; TACTILE-PTH-12MM
FORWARD_SW: SWITCH-MOMENTARY-212MM; TACTILE-PTH-12MM
FRONT_SENSOR: PINHD-1X4; 1X04
IN+: PINHD-1X1; 1X01
IN-: PINHD-1X1; 1X01
LEFT_BACK: PINHD-1X3; 1X03
LEFT_FRONT: PINHD-1X3; 1X03
LEFT_SENSOR: PINHD-1X4; 1X04
LEFT_SW: SWITCH-MOMENTARY-212MM; TACTILE-PTH-12MM
OUT+: PINHD-1X1; 1X01
OUT-: PINHD-1X1; 1X01
PROGRAM_SW: SWITCH-MOMENTARY-212MM; TACTILE-PTH-12MM
RIGHT_BACK: PINHD-1X3; 1X03
RIGHT_FRONT: PINHD-1X3; 1X03
RIGHT_SENSOR: PINHD-1X4; 1X04
RIGHT_SW: SWITCH-MOMENTARY-212MM; TACTILE-PTH-12MM
RV1: POTTRIM; TRIM_POT
SELECT_SW: SWITCH-MOMENTARY-212MM; TACTILE-PTH-12MM
U1: LCD-16X2NOHOLES; LCD-16X2_NOHOLES
U$1: ARDUINO_R3_SHIELD; UNO_R3_SHIELD

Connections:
5V: FRONT_SENSOR.1, LEFT_BACK.2, LEFT_FRONT.2, LEFT_SENSOR.1, OUT+.1, RIGHT_BACK.2, RIGHT_FRONT.2, RIGHT_SENSOR.1, RV1.2 (E), U1.2 (VDD), U1.15 (A)
BACKWARD: BACKWARD_SW.1, U$1.D7
D4: U1.11 (DB4), U$1.A2
D5: U1.12 (DB5), U$1.A3
D6: U1.13 (DB6), U$1.A4
D7: U1.14 (DB7), U$1.A5
E: U1.6 (E), U$1.A1
FORWARD: FORWARD_SW.1, U$1.D8
FRONT_SENSOR: FRONT_SENSOR.2, FRONT_SENSOR.3, U$1.D2
GND: BACKWARD_SW.3 (2), FORWARD_SW.3 (2), FRONT_SENSOR.4, IN-.1, LEFT_BACK.3, LEFT_FRONT.3, LEFT_SENSOR.4, LEFT_SW.3 (2), OUT-.1, PROGRAM_SW.3 (2), RIGHT_BACK.3, RIGHT_FRONT.3, RIGHT_SENSOR.4, RIGHT_SW.3 (2), RV1.3 (A), SELECT_SW.3 (2), U1.1 (VSS), U1.5 (R/W), U1.16 (K), U$1.GND@0, U$1.GND@1
LEFT: LEFT_SW.1, U$1.D10 (*D10)
LEFT_MOTORS: LEFT_BACK.1, LEFT_FRONT.1, U$1.D5 (*D5)
LEFT_SENSOR: LEFT_SENSOR.2, LEFT_SENSOR.3, U$1.D3 (*D3)
unnamed: RV1.1 (S), U1.3 (VO)
PROGRAM: PROGRAM_SW.1, U$1.D12
RIGHT: RIGHT_SW.1, U$1.D9 (*D9)
RIGHT_MOTORS: RIGHT_BACK.1, RIGHT_FRONT.1, U$1.D6 (*D6)
RIGHT_SENSOR: RIGHT_SENSOR.2, RIGHT_SENSOR.3, U$1.D4
RS: U1.4 (RS), U$1.A0
SELECT: SELECT_SW.1, U$1.D11 (*D11)
VCC: IN+.1, U$1.VIN

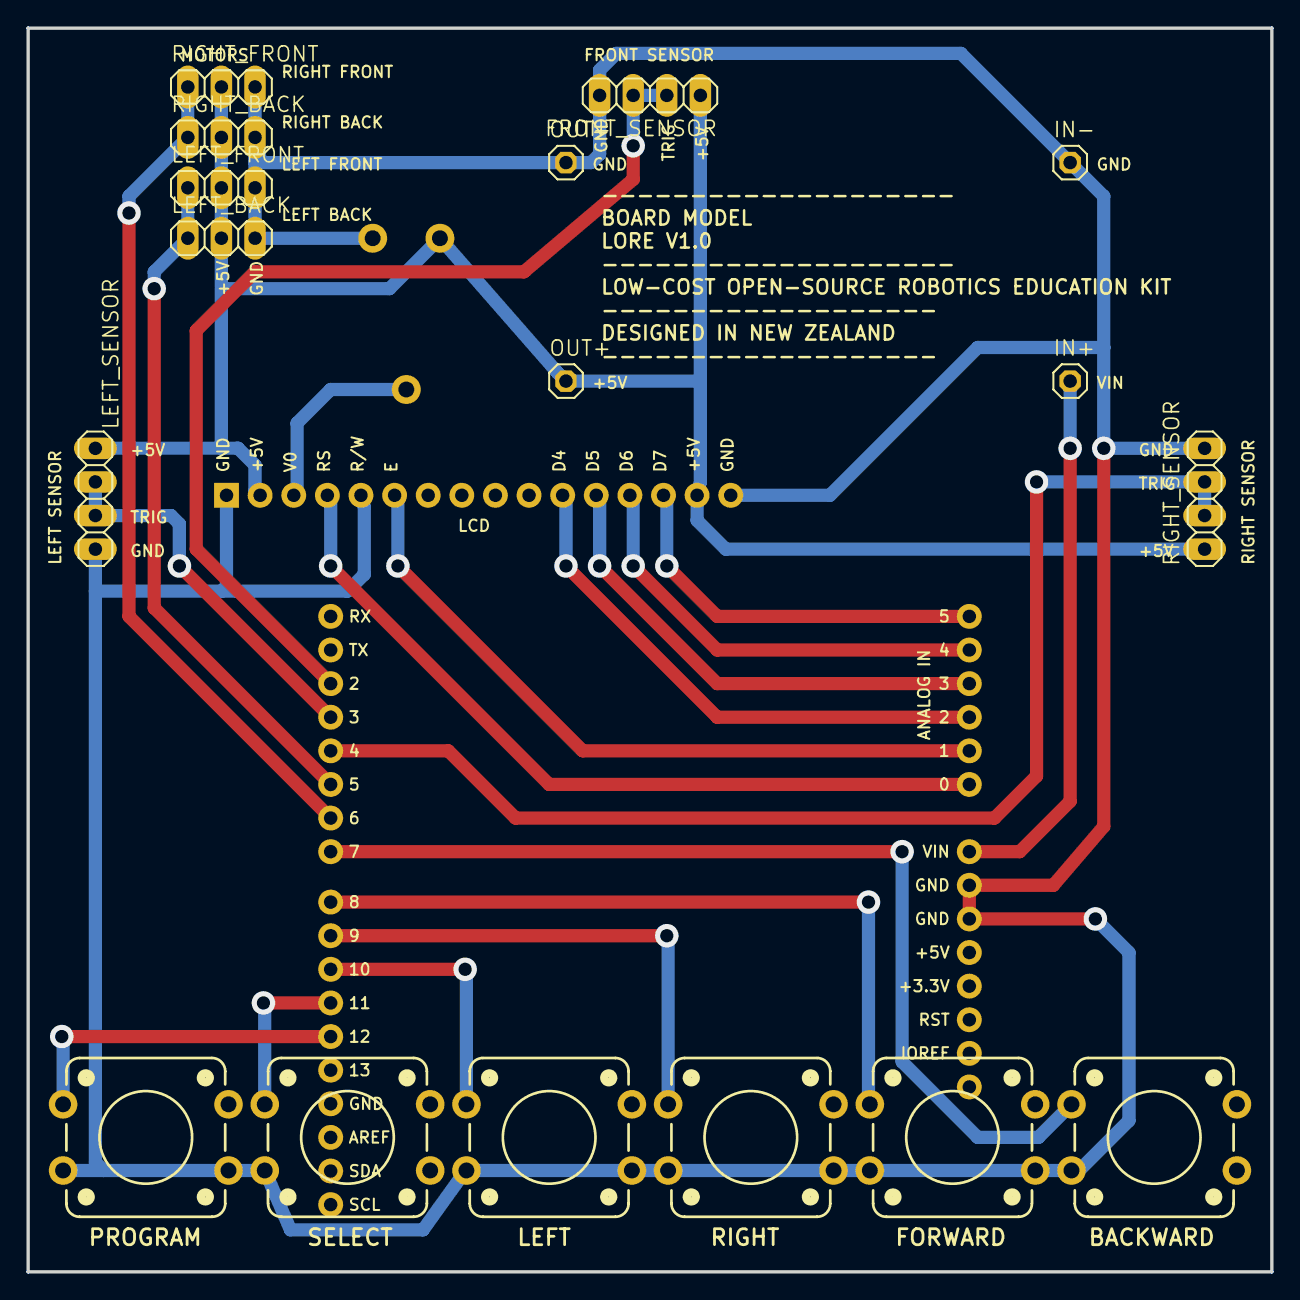
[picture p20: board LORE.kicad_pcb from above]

Board: 2 copper layers, 94.0 x 94.0 mm, 20 parts (0 on the bottom side), 21 nets.

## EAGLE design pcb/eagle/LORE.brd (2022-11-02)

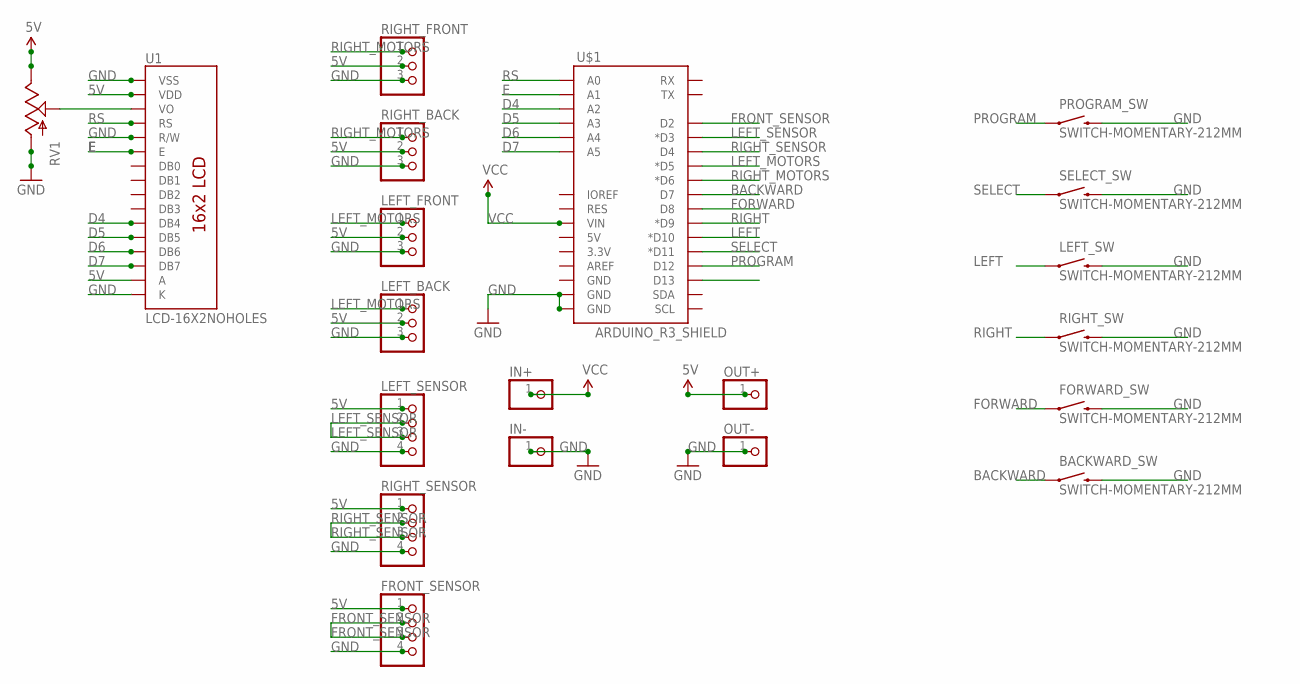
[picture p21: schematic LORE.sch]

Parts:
BACKWARD_SW: SWITCH-MOMENTARY-212MM; TACTILE-PTH-12MM
FORWARD_SW: SWITCH-MOMENTARY-212MM; TACTILE-PTH-12MM
FRONT_SENSOR: PINHD-1X4; 1X04
IN+: PINHD-1X1; 1X01
IN-: PINHD-1X1; 1X01
LEFT_BACK: PINHD-1X3; 1X03
LEFT_FRONT: PINHD-1X3; 1X03
LEFT_SENSOR: PINHD-1X4; 1X04
LEFT_SW: SWITCH-MOMENTARY-212MM; TACTILE-PTH-12MM
OUT+: PINHD-1X1; 1X01
OUT-: PINHD-1X1; 1X01
PROGRAM_SW: SWITCH-MOMENTARY-212MM; TACTILE-PTH-12MM
RIGHT_BACK: PINHD-1X3; 1X03
RIGHT_FRONT: PINHD-1X3; 1X03
RIGHT_SENSOR: PINHD-1X4; 1X04
RIGHT_SW: SWITCH-MOMENTARY-212MM; TACTILE-PTH-12MM
RV1: POTTRIM; TRIM_POT
SELECT_SW: SWITCH-MOMENTARY-212MM; TACTILE-PTH-12MM
U1: LCD-16X2NOHOLES; LCD-16X2_NOHOLES
U$1: ARDUINO_R3_SHIELD; UNO_R3_SHIELD

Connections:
5V: FRONT_SENSOR.1, LEFT_BACK.2, LEFT_FRONT.2, LEFT_SENSOR.1, OUT+.1, RIGHT_BACK.2, RIGHT_FRONT.2, RIGHT_SENSOR.1, RV1.2 (E), U1.2 (VDD), U1.15 (A)
BACKWARD: BACKWARD_SW.1, U$1.D7
D4: U1.11 (DB4), U$1.A2
D5: U1.12 (DB5), U$1.A3
D6: U1.13 (DB6), U$1.A4
D7: U1.14 (DB7), U$1.A5
E: U1.6 (E), U$1.A1
FORWARD: FORWARD_SW.1, U$1.D8
FRONT_SENSOR: FRONT_SENSOR.2, FRONT_SENSOR.3, U$1.D2
GND: BACKWARD_SW.3 (2), FORWARD_SW.3 (2), FRONT_SENSOR.4, IN-.1, LEFT_BACK.3, LEFT_FRONT.3, LEFT_SENSOR.4, LEFT_SW.3 (2), OUT-.1, PROGRAM_SW.3 (2), RIGHT_BACK.3, RIGHT_FRONT.3, RIGHT_SENSOR.4, RIGHT_SW.3 (2), RV1.3 (A), SELECT_SW.3 (2), U1.1 (VSS), U1.5 (R/W), U1.16 (K), U$1.GND@0 (GND), U$1.GND@1 (GND)
LEFT: LEFT_SW.1, U$1.D10 (*D10)
LEFT_MOTORS: LEFT_BACK.1, LEFT_FRONT.1, U$1.D5 (*D5)
LEFT_SENSOR: LEFT_SENSOR.2, LEFT_SENSOR.3, U$1.D3 (*D3)
unnamed: RV1.1 (S), U1.3 (VO)
PROGRAM: PROGRAM_SW.1, U$1.D12
RIGHT: RIGHT_SW.1, U$1.D9 (*D9)
RIGHT_MOTORS: RIGHT_BACK.1, RIGHT_FRONT.1, U$1.D6 (*D6)
RIGHT_SENSOR: RIGHT_SENSOR.2, RIGHT_SENSOR.3, U$1.D4
RS: U1.4 (RS), U$1.A0
SELECT: SELECT_SW.1, U$1.D11 (*D11)
VCC: IN+.1, U$1.VIN

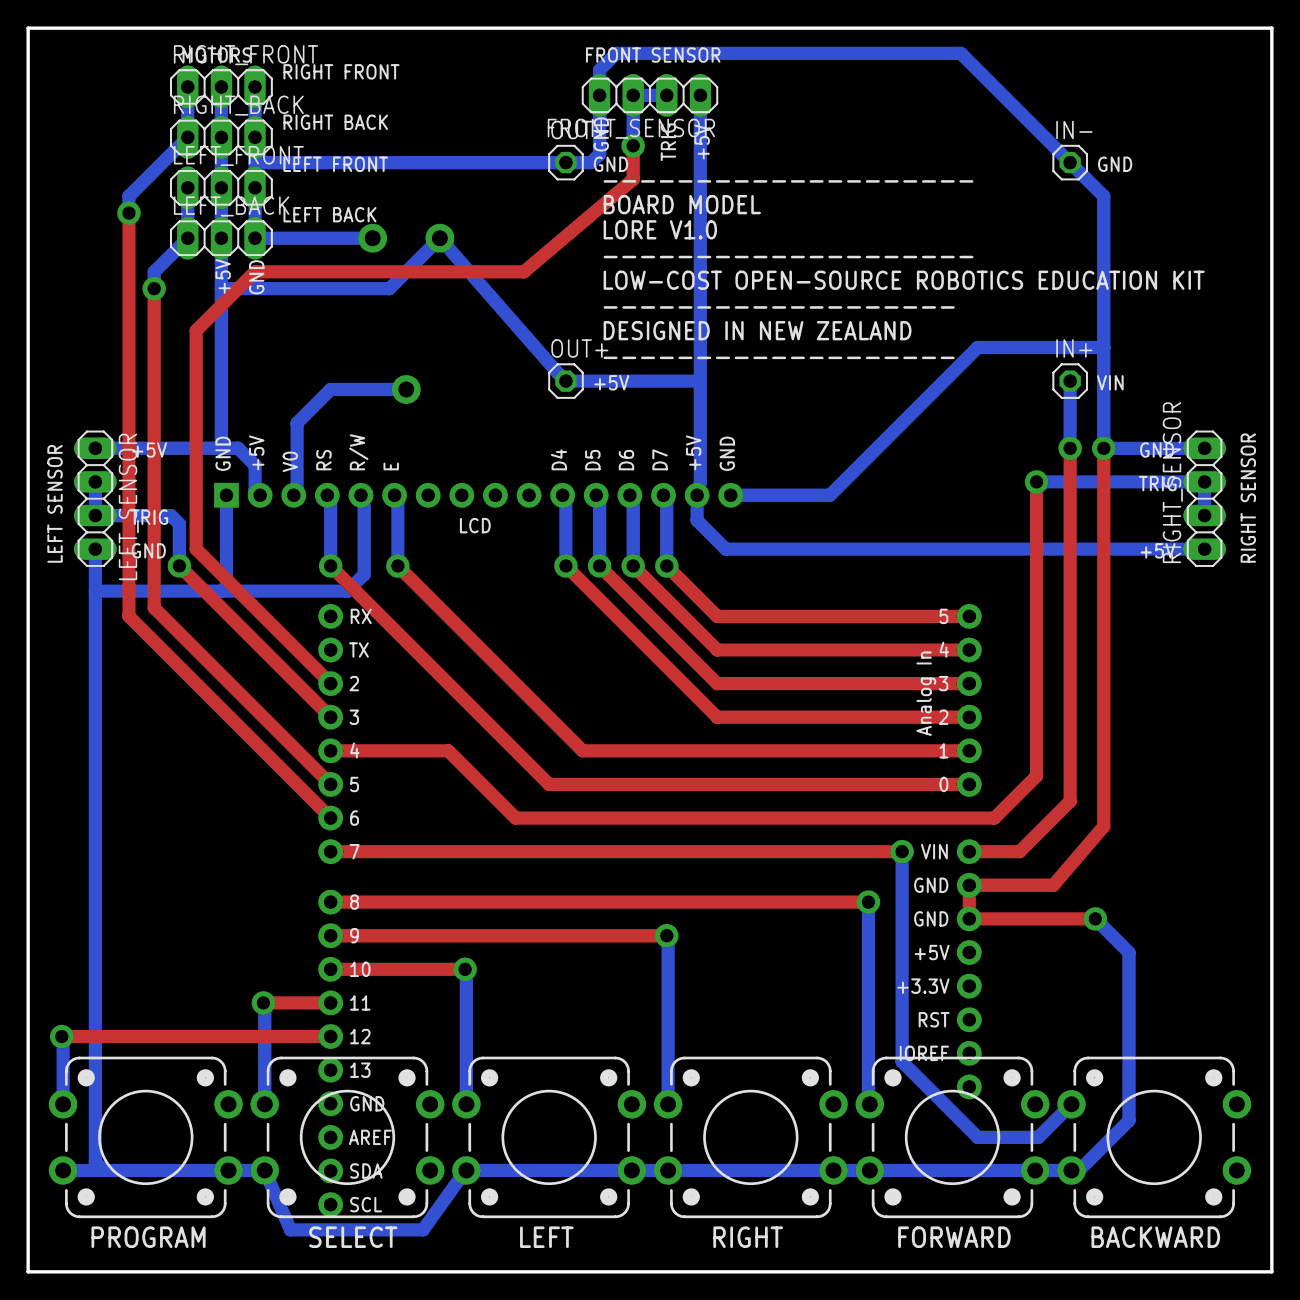
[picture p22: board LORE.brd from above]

Board: 2 copper layers, 94.0 x 94.0 mm, 20 parts (0 on the bottom side), 21 nets.

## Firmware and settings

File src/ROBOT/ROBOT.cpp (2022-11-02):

/*
*	ROBOT.cpp - Libary for controlling the Low-Cost Open-Source Robotic Education (LORE) kit.
*	Version 1.1.
*	Copyright (c) 2014 Dr. Frazer K. Noble. All rights reserved.
*
*	Low-cost Open-source Robotics Educational (LORE) kits are provided "as is" with no warranties whatsoever,
* 	including any warranty of merchantability, non - infringement, fitness for any particular purpose,
* 	or any warranty otherwise arising out of any proposal, specification or sample.
* 	LORE kits (and manufacturers and distributors) disclaim all liability, including liability for infringement of any proprietary rights,
*	relating to use of information in any documents and files and software and no license, express or implied, by LORE kits or otherwise,
*	to any intellectual property rights is granted herein. LORE kits(and manufacturers and distributors) assumes no responsibility or liability
*	for any errors or inaccuracies that may appear in any documentation or files or any software that may be provided.
*	The information in any documents or files is furnished for informational use only, is subject to change without notice,
*	and should not be construed as a commitment by LORE kits(and manufacturers and distributors).
*/

/*
*	The LORE robot is controlled by the following functions.
*
*	The functions are:
*
*	initialise()				- Initialises the LORE robot's pins' states (LOW/HIGH) and direction (INPUT/OUTPUT).
*	move(int direction)			- Moves the robot in the desired direction (LEFT, RIGHT, FORWARD, BACKWARD).
*	readSensor(int sensor)		- Takes a measurement from a sensor (FRONT_SENSOR, LEFT_SENSOR, RIGHT_SENSOR)
*								  and returns the distanc measured.
*	buttonPressed(int button)	- Checks to see if the a button (PROGRAM, SELECT, LEFT, RIGHT, FORWARD, BACKWARD)
*								  is pressed.
*	writeLCD(char* string)		- Writes a series of characters to the LORE robot's LCD panel.
*
*/

#include "ROBOT.h"
#include "string.h"
#include "Arduino.h"		//	Include Arduino.h to gain access to pin and logic level #defines.
#include "Servo.h"			//	Include Servo.h for controlling the LORE robot motors.
#include "LiquidCrystal.h"	//	Include LiquidCrystal.h to be able to write to LORE robot LCD panel.

LiquidCrystal LCD(RS, E, D4, D5, D6, D7);	//	Create an instance of LiquidCrystal Class. Constructor parameters set data pins.
Servo robotLeftMotors, robotRightMotors;	//	Create instances of Servo class. Objects correspond to LORE robot left and right motors.

ROBOT::ROBOT() {

	leftTurnTime = 900;
	rightTurnTime = 900;

	programDebounceTime = 0;
	programState = HIGH;
	programPrevState = HIGH;

	selectDebounceTime = 0;
	selectState = HIGH;
	selectPrevState = HIGH;

	leftDebounceTime = 0;
	leftState = HIGH;
	leftPrevState = HIGH;

	rightDebounceTime = 0;
	rightState = HIGH;
	rightPrevState = HIGH;

	forwardDebounceTime = 0;
	forwardState = HIGH;
	forwardPrevState = HIGH;
	
	backwardDebounceTime = 0;
	backwardState = HIGH;
	backwardPrevState = HIGH;

	frontSensorValue = 1000;
	leftSensorValue = 1000;
	rightSensorValue = 1000;

	debounceDelay = 50;

	programString[50] = 0;
	programSet = 0;
	programSize = 0;

}

bool ROBOT::initialise() {

	pinMode(PROGRAM, INPUT);
	digitalWrite(PROGRAM, HIGH);

	pinMode(SELECT, INPUT);
	digitalWrite(SELECT, HIGH);

	pinMode(LEFT, INPUT);
	digitalWrite(LEFT, HIGH);

	pinMode(RIGHT, INPUT);
	digitalWrite(RIGHT, HIGH);

	pinMode(FORWARD, INPUT);
	digitalWrite(FORWARD, HIGH);

	pinMode(BACKWARD, INPUT);
	digitalWrite(BACKWARD, HIGH);

	robotLeftMotors.attach(LEFT_MOTORS);
	if (robotLeftMotors.attached()) {
		robotLeftMotors.write(127);
	}

	robotRightMotors.attach(RIGHT_MOTORS);
	if (robotRightMotors.attached()) {
		robotRightMotors.write(127);
	}

	return true;

}


bool ROBOT::buttonPressed(int button) {

	if (button == PROGRAM) {

		if (readButton(PROGRAM, programState, programPrevState, programDebounceTime)) {
			return true;
		}

		return false;

	}

	if (button == SELECT) {

		if (readButton(SELECT, selectState, selectPrevState, selectDebounceTime)) {
			return true;
		}

		return false;

	}

	if (button == LEFT) {

		if (readButton(LEFT, leftState, leftPrevState, leftDebounceTime)) {
			return true;
		}

		return false;

	}

	if (button == RIGHT) {

		if (readButton(RIGHT, rightState, rightPrevState, rightDebounceTime)) {
			return true;
		}

		return false;

	}

	if (button == FORWARD) {

		if (readButton(FORWARD, forwardState, forwardPrevState, forwardDebounceTime)) {
			return true;
		}

		return false;

	}

	if (button == BACKWARD) {

		if (readButton(BACKWARD, backwardState, backwardPrevState, backwardDebounceTime)) {
			return true;
		}

		return false;

	}

	return false;

}


bool ROBOT::move(int direction) {

	if (direction == FORWARD) {

		robotLeftMotors.write(0);
		robotRightMotors.write(255);

		unsigned long time = 0;
		time = millis();

		while ((millis() - time) < 1000) {

			if (readSensor(FRONT_SENSOR, frontSensorValue)) {
				if (frontSensorValue < 10)  {
					break;
				}
			}

		}

		robotLeftMotors.write(127);
		robotRightMotors.write(127);

		return true;

	}
	else if (direction == BACKWARD) {

		robotLeftMotors.write(255);
		robotRightMotors.write(0);

		delay(1000);

		robotLeftMotors.write(127);
		robotRightMotors.write(127);

		return true;

	}

	return false;
}

bool ROBOT::turn(int direction) {

	if (direction == LEFT) {

		robotLeftMotors.write(255);
		robotRightMotors.write(255);

		delay(leftTurnTime);

		robotLeftMotors.write(127);
		robotRightMotors.write(127);

		return true;

	}
	else if (direction == RIGHT) {

		robotLeftMotors.write(0);
		robotRightMotors.write(0);

		delay(rightTurnTime);

		robotLeftMotors.write(127);
		robotRightMotors.write(127);

		return true;

	}

	return false;
}

bool ROBOT::clear() {
	
	if (programSet) {
		programSize = 0;
		strcpy(programString, "");
		programString[50] = '\0';
	}

	return true;
}

long ROBOT::measureDistance(int sensor) {

	if (sensor == FRONT_SENSOR) {
		if (readSensor(FRONT_SENSOR, frontSensorValue)) {
			return frontSensorValue;
		}
	}

	if (sensor == LEFT_SENSOR) {
		if (readSensor(LEFT_SENSOR, leftSensorValue)) {
			return leftSensorValue;
		}
	}

	if (sensor == RIGHT_SENSOR) {
		if (readSensor(RIGHT_SENSOR, rightSensorValue)) {
			return rightSensorValue;
		}

	}

	return -1;
}


bool ROBOT::program(int direction) {

	if (programSize >= 49) {

		writeLCD("PROGRAM FULL");

		programString[programSize] = '\0';
		programSet = true;

		return false;

	}

	if (direction == SELECT) {
		programString[programSize] = '\0';
		programSet = true;

		return false;
	}

	if (direction == LEFT) {
		programString[programSize] = 'L';
		programSize++;
		return true;
	}

	if (direction == RIGHT) {
		programString[programSize] = 'R';
		programSize++;
		return true;
	}

	if (direction == FORWARD) {
		programString[programSize] = 'F';
		programSize++;
		return true;

	}

	if (direction == BACKWARD) {
		programString[programSize] = 'B';
		programSize++;
		return true;
	}

	return false;
}
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

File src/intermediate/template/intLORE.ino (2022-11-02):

#include <LiquidCrystal.h>
#include <ROBOT.h>
#include <Servo.h>

ROBOT robot;

void setup()
{

	robot.initialise();

	Serial.begin(9600);

	robot.setTurnTime(LEFT, 900);
	robot.setTurnTime(RIGHT, 900);

}

void loop()
{
	
	if (robot.buttonPressed(PROGRAM)) {
		Serial.print("PROGRAM");

		robot.writeLCD("PROGRAM");

		robot.clear();

		while (true) {

			if (robot.buttonPressed(SELECT)) {
				Serial.print("SELECT");

				robot.writeLCD("SELECT");

				robot.program(SELECT);

				break;
			}

			if (robot.buttonPressed(LEFT)) {
				Serial.print("LEFT");

				robot.writeLCD("LEFT");

				robot.program(LEFT);
			}

			if (robot.buttonPressed(RIGHT)) {
				Serial.print("RIGHT");

				robot.writeLCD("RIGHT");

				robot.program(RIGHT);
			}

			if (robot.buttonPressed(FORWARD)) {
				Serial.print("FORWARD");

				robot.writeLCD("FORWARD");

				robot.program(FORWARD);
			}

			if (robot.buttonPressed(BACKWARD)) {
				Serial.print("BACKWARD");

				robot.writeLCD("BACKWARD");

				robot.program(BACKWARD);
			}

		}

	}


	if (robot.buttonPressed(SELECT)) {
		Serial.print("RUN");

		robot.writeLCD("RUN");

		robot.run();
	}


}

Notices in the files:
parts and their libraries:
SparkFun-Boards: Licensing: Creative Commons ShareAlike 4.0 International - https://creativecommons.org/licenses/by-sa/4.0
